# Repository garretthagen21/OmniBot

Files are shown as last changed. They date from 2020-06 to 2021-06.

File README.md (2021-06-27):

# OmniRobot

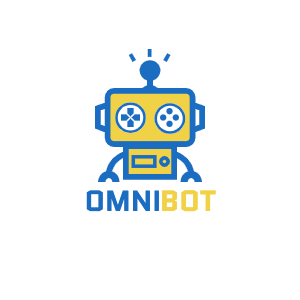
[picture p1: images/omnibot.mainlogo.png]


University of Pittsburgh
ECE Summer 2020 Senior Design Project
Omnidirectional Mobile Robot (OmniRobot / OmniBot)

#### Authors:
* **Grace Brueggman** - Lead for embedded Arduino software
* **Ethan Vander Woude** - Lead for PCB and hardware design
* **Garrett Hagen** - Lead for iOS application and Bluetooth Software  

#### Requirements:
1. The robot must be able to move in all directions: Forward, Backward, Rotate left, Rotate right 
2. The robot must be able to move at variable speeds. 
3. The controls must be controlled remotely using either Bluetooth or HTTP requests. 
4. The controls must also include either a hand gesture or voice recognition method. 
5. The controls must include a simple autopilot mode with obstacle avoidance. 
6. The robot should stop when 4 inches away from an object when operating in autopilot mode. 
7. Design and construction of a custom PCB by the team. 
8. Stay within a $300 budget 

#### Contents of this Repository:
1. Arduino: Embedded Software (Sensor Processing, Bluetooth Wrapper, Motor Control Logic)
2. OmniBot: iOS Application Software
3. Hardware: PCB Schematics, Board Designs, and 3D Printed Parts
4. Images: jpeg images of Pitt and OmniBot logos

####  Videos:
[Usage Walkthrough](https://www.youtube.com/watch?v=svYyvUltygQ&ab_channel=GarrettHagen)

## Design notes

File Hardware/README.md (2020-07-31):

# OmniRobot
Senior Design Mobile Robot Project

## BOM for Omnirobot.pdf
Includes all electrical and hardware components used in final construction of the robot. 
Has pricing per unit, quatity, part number, and description of component use.
  
## Breadboard Circuit.pdf
Original pin connections used on breadboard version of circuit. This was later changed as all ultrasonic sensors and the Bluetooth module was added.

## ConnectionPinout.SchDoc
Altium Designer schematic with all pin connections to external pins, like motors, ultrasonic sensors, Bluetooth module, etc.

## SDP1.PcbDoc
Altium Designer PCB. Three viewing options:
1. Component outlines
2. Trace Connections
3. 3D View

## Senior Design.PrjPcb
Altium Design project file.

## SeniorDesignPCB.SchDoc
Altium Designer schematic for power connections and ATmega328PU and L293NE (motor driver ICs).

## Verification Testing.xlsx
Excel document with three sheets, each with data from various tests.
Sheet 1: Stopping distance evaluation
Sheet 2: Power consumption and battery longevity
Sheet 3: Speed analysis

## CAD
CAD drawings in the form of .stl and .ipt Inventor files
Contains both single mount version and tri-mount version of
ultrasonic sensor mounts

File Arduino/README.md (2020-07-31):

# OmniRobot/Arduino

Embedded Software

Contents:

1. Bluetooth - Serial Reading
2. OmniBLE - Bluetooth Wrapper
3. OmniBLETest - testing of OmniBLE
4. OmniControl - sensor processing and control logic
5. OmniControlTest - isolated function integration testing
6. BLELatencyTesting - Files for calculating Bluetooth latency

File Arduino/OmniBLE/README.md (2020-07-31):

# OmniBLE

Bluetooth Low Energy API Library for Arduino. Handles sending, and recieiving/parsing data

#### Contents
1. OmniBLE.h - Function declarations for API
2. OmniBLE.cpp - Implmentation of functions declared in OmniBLE.h

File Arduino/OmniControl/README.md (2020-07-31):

# OmniRobot/Arduino/OmniControl

Program to upload to PCB during normal operation

Contents of OmniControl.ino: 

Motor Control:
go_Advance()
go_Back()
go_Right()
go_Left()
stop_Stop()
enable_Motors()
disable_Motors()

Ultrasonic Sensor Processing:
watch_FL()
watch_FR()
watch_L()
watch_R()

Modes:
obstacle_avoidance_mode()
joystick_gesture_mode()

General:
setup()
loop()

Contents of configuration.h:
constant declarations variable declarations pin numbers

Contents of OmniBLE.h
Bluetooth wrapper functionality

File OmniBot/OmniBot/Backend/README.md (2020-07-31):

# Backend

Contains files that implement functionality for business logic and backend objects

#### Contents
1. Alerts.swift - Utility class for UI alerts and information popups
2. BluetoothSerial.swift - API that abstracts Blutooth operations
3. Extensions.swift - File that contains various class extensions
4. MBProgressHUD.h/m - UI popup source code
5. RobotState.swift - Global class that contains current velocity, turning, and autopilot status of robot
6. UserSettings.swift - API that manages loading and storing user configurations to/from storage
7. Protocols.swift - File that contains various protocols (interfaces) to be implemented
8. OmniBot-Bridging-Header.h - Requried file to include Obj-c source code in app build

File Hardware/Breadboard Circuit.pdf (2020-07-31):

Pin Connections

ATmega Pin | Wire Color | Arduino Program
Other | Other Pin
| | Bluetooth Module
2 | Yellow | RX
3 | Orange | TX
| Red | 5V
| Black | GND

Ultrasonic Sensor (Front)

11 | Blue | D4
12 | Purple | D6
| Red | 5V
| Black | GND

Ultrasonic Sensor (Left)

13 | Gray | D7
14 | White | D8
| Red | 5V
| Black | GND

Ultrasonic Sensor (Back)

18 | Brown | D12
19 | Green | D13
| Red | 5V
| Black | GND

Ultrasonic Sensor (Right)

23 | Purple | A0

24 | Gray | A1
| White | 5V
| Black | GND

Right Motors

28 | A5 | 4A | 15
27 | A4 | 3A | 10
26 | A3 | 3,4 Enable | 9

Left Motors

15 | D9 | 2A | 7
16 | D10 | 1A | 2
17 | D11 | 1,2 Enable | 1

Coding Board

1 | Reset | 1
2 | RX | 2
3 | TX | 3
| 5V | 4
| GND | 5

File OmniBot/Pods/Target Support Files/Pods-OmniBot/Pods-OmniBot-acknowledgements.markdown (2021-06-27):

# Acknowledgements
This application makes use of the following third party libraries:

## BRHJoyStickView

Copyright 2018 Brad Howes

Permission is hereby granted, free of charge, to any person obtaining a copy of this software and associated
documentation files (the "Software"), to deal in the Software without restriction, including without limitation
the rights to use, copy, modify, merge, publish, distribute, sublicense, and/or sell copies of the Software, and
to permit persons to whom the Software is furnished to do so, subject to the following conditions:

The above copyright notice and this permission notice shall be included in all copies or substantial portions of
the Software.

THE SOFTWARE IS PROVIDED "AS IS", WITHOUT WARRANTY OF ANY KIND, EXPRESS OR IMPLIED, INCLUDING BUT NOT LIMITED TO
THE WARRANTIES OF MERCHANTABILITY, FITNESS FOR A PARTICULAR PURPOSE AND NONINFRINGEMENT. IN NO EVENT SHALL THE
AUTHORS OR COPYRIGHT HOLDERS BE LIABLE FOR ANY CLAIM, DAMAGES OR OTHER LIABILITY, WHETHER IN AN ACTION OF
CONTRACT, TORT OR OTHERWISE, ARISING FROM, OUT OF OR IN CONNECTION WITH THE SOFTWARE OR THE USE OR OTHER
DEALINGS IN THE SOFTWARE.

## CocoaLumberjack

BSD 3-Clause License

Copyright (c) 2010-2021, Deusty, LLC
All rights reserved.

Redistribution and use in source and binary forms, with or without modification, are permitted provided that the following conditions are met:

1. Redistributions of source code must retain the above copyright notice, this list of conditions and the following disclaimer.

2. Redistributions in binary form must reproduce the above copyright notice, this list of conditions and the following disclaimer in the documentation and/or other materials provided with the distribution.

3. Neither the name of Deusty nor the names of its contributors may be used to endorse or promote products derived from this software without specific prior written permission of Deusty, LLC.

THIS SOFTWARE IS PROVIDED BY THE COPYRIGHT HOLDERS AND CONTRIBUTORS "AS IS" AND ANY EXPRESS OR IMPLIED WARRANTIES, INCLUDING, BUT NOT LIMITED TO, THE IMPLIED WARRANTIES OF MERCHANTABILITY AND FITNESS FOR A PARTICULAR PURPOSE ARE DISCLAIMED. IN NO EVENT SHALL THE COPYRIGHT HOLDER OR CONTRIBUTORS BE LIABLE FOR ANY DIRECT, INDIRECT, INCIDENTAL, SPECIAL, EXEMPLARY, OR CONSEQUENTIAL DAMAGES (INCLUDING, BUT NOT LIMITED TO, PROCUREMENT OF SUBSTITUTE GOODS OR SERVICES; LOSS OF USE, DATA, OR PROFITS; OR BUSINESS INTERRUPTION) HOWEVER CAUSED AND ON ANY THEORY OF LIABILITY, WHETHER IN CONTRACT, STRICT LIABILITY, OR TORT (INCLUDING NEGLIGENCE OR OTHERWISE) ARISING IN ANY WAY OUT OF THE USE OF THIS SOFTWARE, EVEN IF ADVISED OF THE POSSIBILITY OF SUCH DAMAGE.

Generated by CocoaPods - https://cocoapods.org

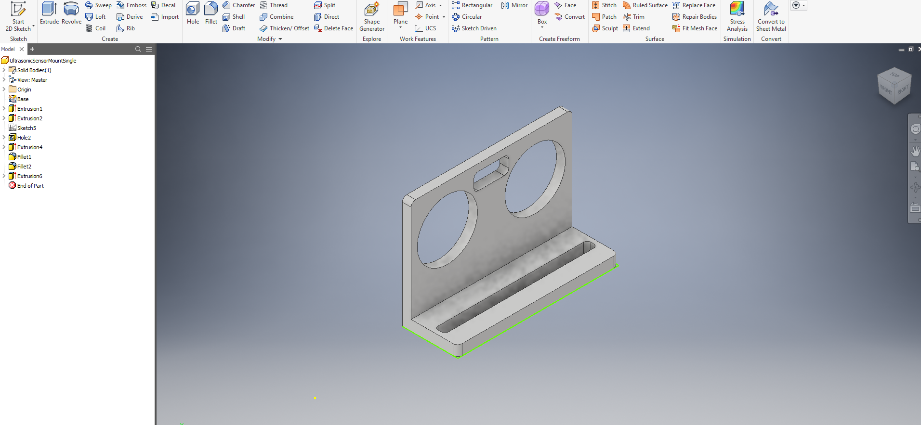
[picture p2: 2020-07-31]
Hardware/CAD/SensorMountSingleImage.PNG

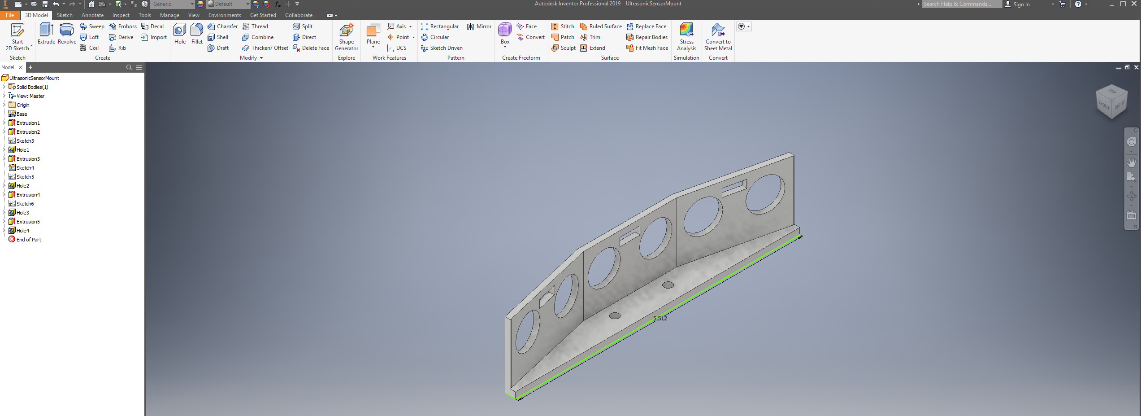
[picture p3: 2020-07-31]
Hardware/CAD/SensorMountImage.PNG

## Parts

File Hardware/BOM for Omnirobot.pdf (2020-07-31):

Name | Quantity | Price | Vendor | Purpose
ATmega328PU | 1 | $2.13 | Digi-Key | Central microcontroller for interpretting app signals and control logic | $2.13 Motor Driver | 2 | $3.68 | Digi-Key | Motor driver chips to control speed and direction of motor rotation | $7.36
16 MHz Crystal Oscillator | 1 | $0.69 | Digi-Key | Used by the ATmega chip to determine internal clock | $0.69
10 kOhm Resistor | 1 | $0.04 | Digi-Key | Resistor between reset pin of ATmega and 5V | $0.04
22pF Ceramic Capacitors
5V Voltage Regulator
0.33 uF Ceramic Capacitors
2 | $0.23 | Digi-Key | Capacitors which tie crystal oscillator to GND | $0.46
2 | $0.62 | Digi-Key | Regulators for 5V needed by ATmega and motor drivers | $1.24
2 | $0.23 | Digi-Key | Stabalize input voltage from batteries for voltage regulators | $0.45
Toggle Switch DPDT | 1 | $2.95 | Digi-Key | Switch between battery pack and PCB | $2.95
AA Batteries (20 pack)
8 | $0.85 | Amazon | Power source for entire robot | $6.79
Battery Holder with On/Off Switch | 1 | $8.00 | Amazon | Configures 8 AA batteries to about around 12V | $8.00
16pos IC Dip Socket
2 | $0.83 | Digi-Key | Solder sockets for motor drivers | $1.66
28pos IC Dip Socket | 1 | $1.44 | Digi-Key | Solder sockets for ATmega | $1.44
HM-10 Bluetooth Module | 1 | $10.59 | Amazon | bluetooth module for communication between ATmega and phone application | $10.59
Ultrasonic Sensor HC-SR04 x 4 | 1 | $11.79 | Amazon | Package of 4 HC-SR04 ultrasonic sensors | $11.79 Wire Set | 1 | $15.83 | Amazon | Wire connection between motors, ultrasonic sensors, and bluetooth module to PCB | $15.83
Chassis Kit (Chassis, 4 DC TT Motors, 4 Wheels) | 1 | $26.42 | Amazon | Main robot body, motors, and wheels | $26.42 M3-0.5 X 25MM Screws | 1 | $3.27 | Amazon | Screws to attaching standoffs to PCB and Chassis | $3.27 M3 X 60MM Screw Spacers | 1 | $11.76 | Amazon | Standoffs for attachment of PCB to robot chassis | $11.76
PCB Print | 1 | $6.65 | ALLPCB | PCB print from outsourced comapny | $6.65
Total Cost of Production | $119.52

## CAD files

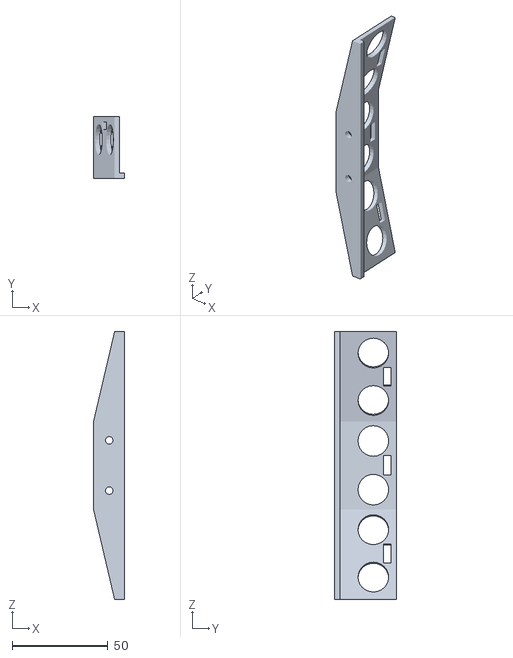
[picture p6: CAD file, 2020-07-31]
Hardware/CAD/UltrasonicSensorMount.stl
16.0 x 32.5 x 140.0

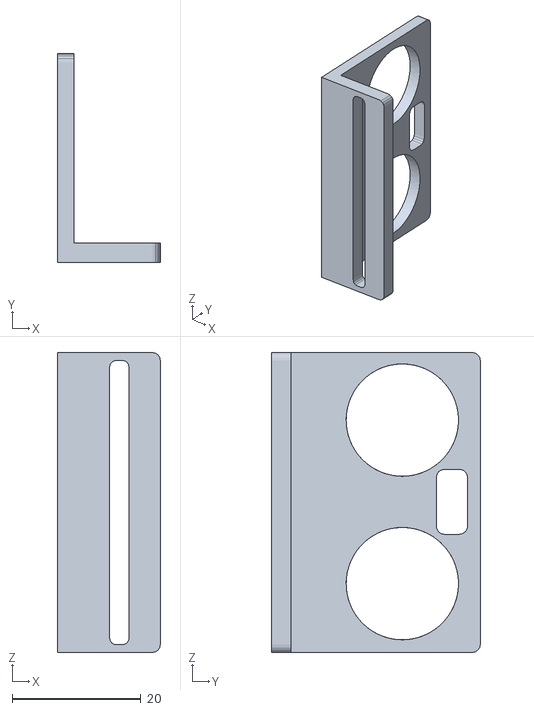
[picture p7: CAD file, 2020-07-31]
Hardware/CAD/UltrasonicSensorMountSingle.stl
16.0 x 32.5 x 46.7

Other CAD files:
Hardware/CAD/OldVersions/UltrasonicSensorMountSingle.0001.ipt
Hardware/CAD/UltrasonicSensorMount.ipt
Hardware/CAD/UltrasonicSensorMountSingle.ipt

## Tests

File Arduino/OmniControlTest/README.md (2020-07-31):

OmniRobot/Arduino/OmniControlTest

Program to upload to PCB during integration testing

Contents of OmniControlTest.ino - 

Motor Control:
go_Advance()
go_Back()
go_Right()
go_Left()
stop_Stop()
enable_Motors()
disable_Motors()

Ultrasonic Sensor Processing:
watch_FL()
watch_FR()
watch_L()
watch_R()

Modes:
obstacle_avoidance_mode()
joystick_gesture_mode()

Testing:
testForwardSlow()
testForwardMedium()
testForwardFast()
testBackwards()
testLeft()
testRight()
testStop()
  
testFLUS()
testFRUS()
testLUS()
testRUS()

General:
setup()
loop()

Contents of configuration.h
constant declarations
variable declarations
pin numbers

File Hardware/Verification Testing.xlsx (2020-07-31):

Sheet: Stop Accuracy
Distance Test |  |  | Speed(PWM)
Run Number | 80 | 100 | 120 | 140 | 160
1 | 4.25 | 4.25 | 3.75 | 4 | 3
2 | 4.5 | 4.5 | 4 | 3.5 | 3.25
3 | 5 | 4 | 4.5 | 3.75 | 3.25
4 | 5 | 4 | 3.75 | 4 | 3
5 | 5 | 4 | 5 | 4 | 3
5 | 5 | 4.25 | 4 | 3.75 | 3.25
6 | 4.5 | 4 | 4 | 3.5 | 3
7 | 4.75 | 4.5 | 4 | 3.75 | 3
8 | 4.75 | 4.75 | 4 | 4 | 3.25
9 | 5 | 4.75 | 4.25 | 4 | 2.5
10 | 4.75 | 4.75 | 5 | 3.5 | 2.5
Average (inches) | 4.772727273 | 4.340909091 | 4.204545455 | 3.795454545 | 3

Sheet: Power Calculations
Speed (PWM) | 60 | 120 | 240
Maximum Load Current (mA) | 431 | 675 | 1216
Nominal Battery Voltage | 12 | 12 | 12
Voltage at Testing | 11.84 | 11.84 | 11.84
Expected mAh | 4500 | 4500 | 4500
Total Expected Runtime (Hr) | 10.44083527 | 6.666666667 | 3.700657895
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

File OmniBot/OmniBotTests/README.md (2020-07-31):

# OmniBotTests

There are no automated backend tests for this project

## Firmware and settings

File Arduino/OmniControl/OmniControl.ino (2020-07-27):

#include "configuration.h"
#include <OmniBLE.h>

/*setup Bluetooth module*/
OmniBLE botBT(5,6); // Pins: rx, rt
  
/*motor control*/
void go_Advance(void) //Forward
{
  enable_Motors();
  analogWrite(dir1PinL,spdL);
  digitalWrite(dir2PinL,LOW);
  analogWrite(dir1PinR,spdR);
  digitalWrite(dir2PinR,LOW);
}
void go_Right()  //Turn right
{
  enable_Motors();
  analogWrite(dir1PinL,spdL);
  digitalWrite(dir2PinL,LOW);
  digitalWrite(dir1PinR,LOW);
  analogWrite(dir2PinR,spdR);
}
void go_Left()  //Turn left
{
  enable_Motors();
  digitalWrite(dir1PinL,LOW);
  analogWrite(dir2PinL,spdL);
  analogWrite(dir1PinR,spdR);
  digitalWrite(dir2PinR,LOW);
}
void go_Back()  //Reverse
{
  enable_Motors();
  digitalWrite(dir1PinL,LOW);
  analogWrite(dir2PinL,spdL);
  digitalWrite(dir1PinR,LOW);
  analogWrite(dir2PinR,spdR);
}
void stop_Stop()    //Stop
{
  disable_Motors();
  digitalWrite(dir1PinL,LOW);
  digitalWrite(dir2PinL,LOW);
  digitalWrite(dir1PinR,LOW);
  digitalWrite(dir2PinR,LOW);
}

/*enable motor speed */
void enable_Motors()
{
  digitalWrite(enableL,HIGH); 
  digitalWrite(enableR,HIGH);   
}

/*disable motor speed */
void disable_Motors()
{
  digitalWrite(enableL,LOW); 
  digitalWrite(enableR,LOW);   
}

/*detection of FL ultrasonic distance*/
int watch_FL(){
  long echo_distance;
  digitalWrite(Trig_PIN_FL,LOW);
  delayMicroseconds(5);                                                                              
  digitalWrite(Trig_PIN_FL,HIGH);
  delayMicroseconds(15);
  digitalWrite(Trig_PIN_FL,LOW);
  echo_distance=pulseIn(Echo_PIN_FL,HIGH);
  echo_distance=echo_distance*0.01657; //how far away is the object in cm
//  Serial.println((int)echo_distance);
  return round(echo_distance);
}

/*detection of FR ultrasonic distance*/
int watch_FR(){
  long echo_distance;
  digitalWrite(Trig_PIN_FR,LOW);
  delayMicroseconds(5);                                                                              
  digitalWrite(Trig_PIN_FR,HIGH);
  delayMicroseconds(15);
  digitalWrite(Trig_PIN_FR,LOW);
  echo_distance=pulseIn(Echo_PIN_FR,HIGH);
  echo_distance=echo_distance*0.01657; //how far away is the object in cm
//  Serial.println((int)echo_distance);
  return round(echo_distance);
}

/*detection of L ultrasonic distance*/
int watch_L(){
  long echo_distance;
  digitalWrite(Trig_PIN_L,LOW);
  delayMicroseconds(5);                                                                              
  digitalWrite(Trig_PIN_L,HIGH);
  delayMicroseconds(15);
  digitalWrite(Trig_PIN_L,LOW);
  echo_distance=pulseIn(Echo_PIN_L,HIGH);
  echo_distance=echo_distance*0.01657; //how far away is the object in cm
//  Serial.println((int)echo_distance);
  return round(echo_distance);
}

/*detection of FL ultrasonic distance*/
int watch_R(){
  long echo_distance;
  digitalWrite(Trig_PIN_R,LOW);
  delayMicroseconds(5);                                                                              
  digitalWrite(Trig_PIN_R,HIGH);
  delayMicroseconds(15);
  digitalWrite(Trig_PIN_R,LOW);
  echo_distance=pulseIn(Echo_PIN_R,HIGH);
  echo_distance=echo_distance*0.01657; //how far away is the object in cm
//  Serial.println((int)echo_distance);
  return round(echo_distance);
}

/*Obstacle Avoidance Mode*/
void obstacle_avoidance_mode(){  
  dis_FL = watch_FL();
  dis_FR = watch_FR();
  dis_L = watch_L();
  dis_R = watch_R();
  
  if ( (dis_FL <= up_bound) || (dis_FR <= up_bound) ){
    go_Back();
    delay(back_time);
    stop_Stop();
    if (dis_L <= dis_R){
      go_Right();
      while( (dis_FL <= up_bound + extra_space) || (dis_FR <= up_bound + extra_space) || (dis_L <= up_bound)){
        delay(turn_time);
        dis_L = watch_L();
        dis_FL = watch_FL();
        dis_FR = watch_FR();
      }
      stop_Stop();
    }
    else if (dis_R < dis_L){
      go_Left();
      while( (dis_FL <= up_bound + extra_space) || (dis_FR <= up_bound + extra_space) || (dis_R <= up_bound)){
        delay(turn_time);
        dis_R = watch_R();
        dis_FL = watch_FL();
        dis_FR = watch_FR();
      }
      stop_Stop();      
    }
  }
  else {
    go_Advance();
  }
}

/* Joystick Mode */
void joystick_gesture_mode(){
    char cmd;
    
    cmd = botBT.cardinalDirection();
    switch(cmd){
      case 'N':
        go_Advance();
        break;
      case 'S':
        go_Back();
        break;
      case 'W':
        go_Left();
        break;
      case 'E':
        go_Right();
        break;
   }
}

void setup() {  
  /*setup L298N pin mode*/
  pinMode(dir1PinL, OUTPUT); 
  pinMode(dir2PinL, OUTPUT); 
  pinMode(enableL, OUTPUT);  
  pinMode(dir1PinR, OUTPUT);
  pinMode(dir2PinR, OUTPUT); 
  pinMode(enableR, OUTPUT); 
  stop_Stop(); // stop move
  
  /*init HC-SR04*/
  pinMode(Trig_PIN_FL, OUTPUT); 
  pinMode(Echo_PIN_FL, INPUT); 
  digitalWrite(Trig_PIN_FL, LOW);

  pinMode(Trig_PIN_FR, OUTPUT); 
  pinMode(Echo_PIN_FR, INPUT); 
  digitalWrite(Trig_PIN_FR, LOW);

  pinMode(Trig_PIN_L, OUTPUT); 
  pinMode(Echo_PIN_L, INPUT); 
  digitalWrite(Trig_PIN_L, LOW);

  pinMode(Trig_PIN_R, OUTPUT); 
  pinMode(Echo_PIN_R, INPUT); 
  digitalWrite(Trig_PIN_R, LOW);
  
  /*baud rate*/
  Serial.begin(9600);

  /*bluetooth wrapper*/
  botBT.printDebugToSerial = false;
  botBT.begin(9600);

  // Note: This sets the broadcasting name of the HM-10 bluetooth module. We only need to do this once
  botBT.setPeripheralName("OmniBot");
}

void loop() {
  dis_FL = watch_FL();
  dis_FR = watch_FR();
  dis_L = watch_L();
  dis_R = watch_R();
  
  // Update our botBT with the latest data
  botBT.sync();
  
  spd = round(botBT.speedValue()*max_PWM);
  angle = round(botBT.turnValue()*90);

  if(angle >= 0){
    spdL = spd;
    spdR = cos(angle)*spd;
  }
  if(angle < 0){
    spdL = -cos(angle)*spd;
    spdR = spd;
  }
  
  if (spdL < 50 && spdL > 0){
    spdL = 50;
  }
  if (spdR < 50 && spdR > 0){
    spdR = 50;
  }
    
  if(botBT.autopilotValue()){
      obstacle_avoidance_mode();
  }
  else {
      joystick_gesture_mode();
  }
  
  // Send sensor vals to device. 
  // Note we should only send a message when these change to avoid clobbering bluetooth channel
  float sensorProximities[NUM_SONIC_SENSORS] = {float(dis_FL), float(dis_FR), float(dis_L), float(dis_R)};
  botBT.sendProximityMeasurements(sensorProximities,NUM_SONIC_SENSORS);
}

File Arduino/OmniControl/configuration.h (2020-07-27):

/*Declare L298N Dual H-Bridge Motor Controller directly since there is not a library to load.*/
//Define L298N Dual H-Bridge Motor Controller Pins
#define dir1PinL  10    //Motor direction
#define dir2PinL  9    //Motor direction
#define enableL 2    // Needs to be a PWM pin to be able to control motor speed

#define dir1PinR  11    //Motor direction
#define dir2PinR  3   //Motor direction
#define enableR 4    // Needs to be a PWM pin to be able to control motor speed

#define Echo_PIN_FL    A2 // Ultrasonic Echo pin connect to D11
#define Trig_PIN_FL    8  // Ultrasonic Trig pin connect to D12

#define Echo_PIN_FR    A3 // Ultrasonic Echo pin connect to D11
#define Trig_PIN_FR    7  // Ultrasonic Trig pin connect to D12

#define Echo_PIN_L    A4 // Ultrasonic Echo pin connect to D11
#define Trig_PIN_L    12  // Ultrasonic Trig pin connect to D12

#define Echo_PIN_R    A5 // Ultrasonic Echo pin connect to D11
#define Trig_PIN_R    13  // Ultrasonic Trig pin connect to D12


//#define SPEED  200     //both sides of the motor speed
//#define BACK_SPEED1  100     //back speed
//#define BACK_SPEED2  150     //back speed
         
const int sidedistancelimit = 30; //minimum distance in cm to obstacles at both sides (the car will allow a shorter distance sideways)
const int NUM_SONIC_SENSORS = 4;
const int numcycles = 0;
const int turn_time = 100; //Time the robot spends turning (miliseconds)
const int back_time = 300; //Time the robot spends turning (miliseconds)
const int up_bound = 10; //cm
const int lo_bound = 2; //cm
const int max_PWM = 150;
const int extra_space = 5; //cm

int distance, thereis, dis_FL, dis_FR, dis_L, dis_R, angle, spd, spdL, spdR;

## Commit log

2020-05-18 object avoidance and bluetooth
    [configuration.h]
2020-06-30 finished first pass at omni robot api. and got connectivity working. Need to smooth out sensor input
    [configuration.h]
2020-06-30 added arduino library and ios
    [configuration.h]
2020-07-07 staged OmniControl from bluetooth input and add obstacle avoidance for 4 ultrasonic sensors
    [configuration.h]
2020-07-08 added the correct bluetooth spped direction cmds, but still work compile
    [configuration.h]
2020-07-12 fixed omniBLE lib reference
    [OmniControl.ino]
2020-07-17 config cleanup
    [configuration.h]
2020-07-18 config cleanup and omnicontroltest created
    [configuration.h]
2020-07-18 update config pinout
    [configuration.h]
2020-07-18 update pin config
    [configuration.h]
2020-07-18 reworked basic motor controls
    [configuration.h]
2020-07-26 speed variance depending on angle
    [configuration.h]
2020-07-27 updating files with minor changes
    [configuration.h]
2020-07-27 add obstacle avoidance test
    [OmniControl.ino, OmniControlTest.ino]
2020-07-27 alternative obstacle avoidance mode with whiels tatement
    [configuration.h]
2020-07-27 add side sensor checks on while turn
2020-07-27 improved avoidance mode in control
    [configuration.h]
2020-07-31 removed faulty obstacle avoidance mode
    [OmniControlTest.ino]
2020-07-31 added cad files and images
    [UltrasonicSensorMount.ipt, UltrasonicSensorMount.stl, UltrasonicSensorMountSingle.0001.ipt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]
2020-07-31 renamed folder
    [UltrasonicSensorMount.ipt, UltrasonicSensorMount.stl, UltrasonicSensorMountSingle.0001.ipt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]
2020-09-23 Added untracked files
    [UltrasonicSensorMount.ipt, UltrasonicSensorMount.stl, UltrasonicSensorMountSingle.0001.ipt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]
